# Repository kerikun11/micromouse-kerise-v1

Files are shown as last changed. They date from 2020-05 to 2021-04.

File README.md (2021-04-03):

# MicroMouse KERISE v1

クラッシクサイズマイクロマウス

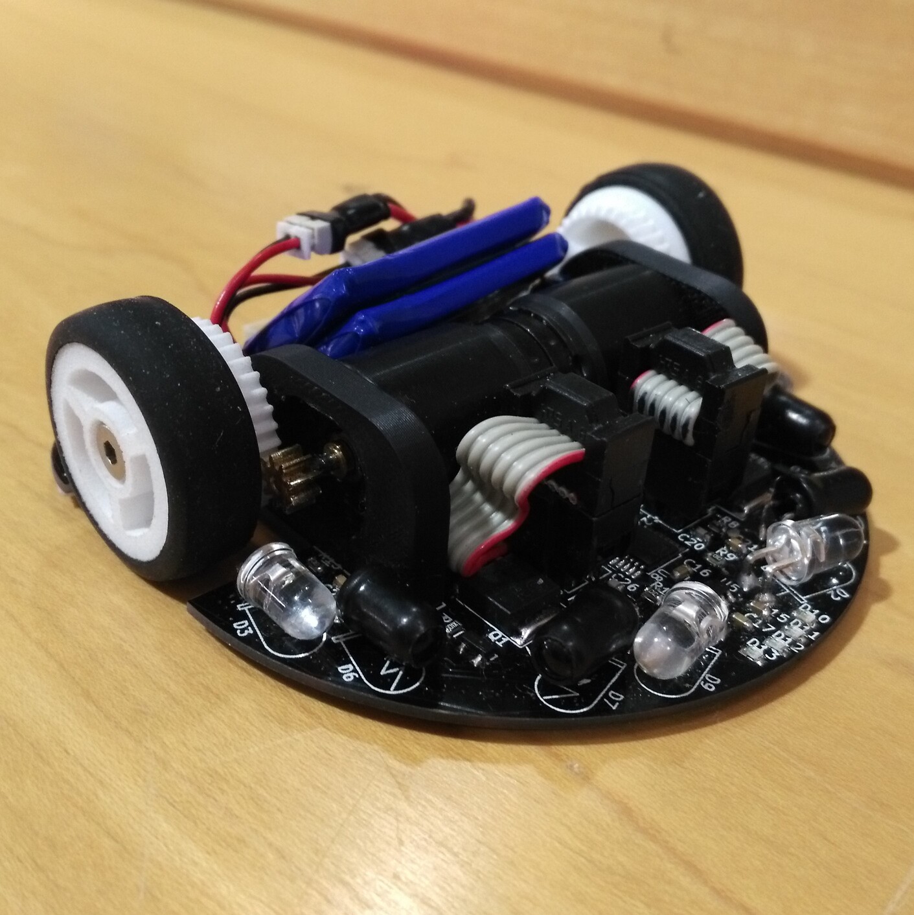
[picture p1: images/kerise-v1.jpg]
KERISE v1


## 戦績

- 第37回全日本マイクロマウス大会2016
  - クラッシック競技フレッシュマンクラス予選10位
  - クラッシック競技フレッシュマンクラス決勝9位

## スペック

| 部品 | 型番 | 備考 |
| :--- | :--- | :--- |
| モーター | 1717T006SR | 17mm x 17mm |
| エンコーダ | IEH2-1024 | 1024パルス モーター直結 |
| マイコン | STM32F405RG | 168MHz |
| 赤外線LED | VSLY5850 | 波長850mm 直径5mm |
| フォトダイオード | SFH213FA | 波長900nm 直径5mm |
| モータードライバ | DRV8835 | 最大電流3A |
| 6軸センサ | MPU6500 | 3軸ジャイロ+3軸加速度 |
| バッテリー | LG325-0120-1S-M | 3.7V 25C 120mAh 1S |

## 回路設計

- KiCad

## 開発環境

- mbed RTOS

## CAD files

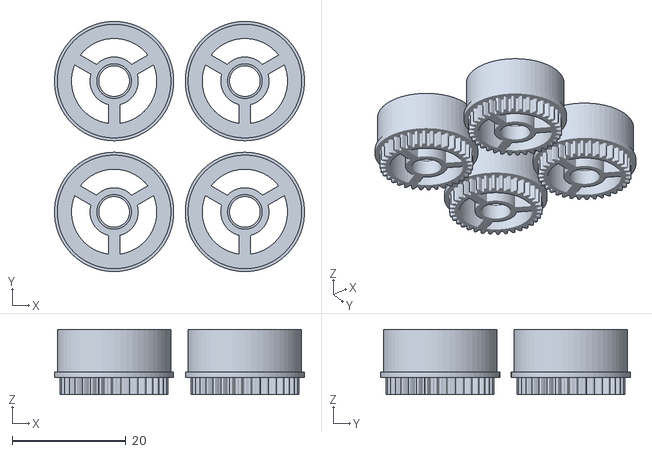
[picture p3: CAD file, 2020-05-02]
3dprint/wheel-2set.stl
44.0 x 44.0 x 11.5

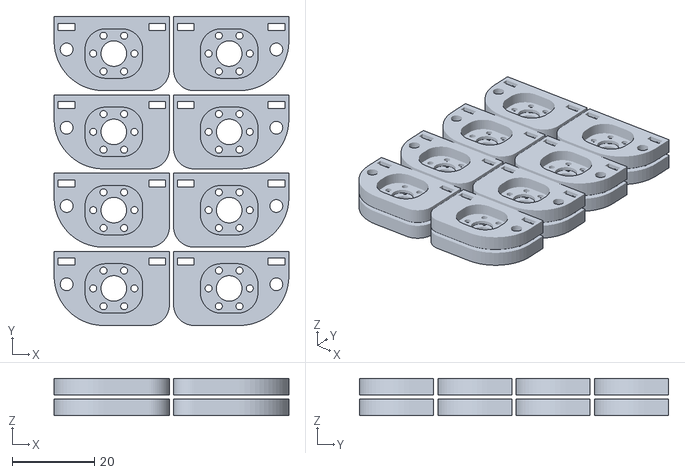
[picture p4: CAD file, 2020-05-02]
3dprint/mounter-8set.stl
57.0 x 75.0 x 9.00

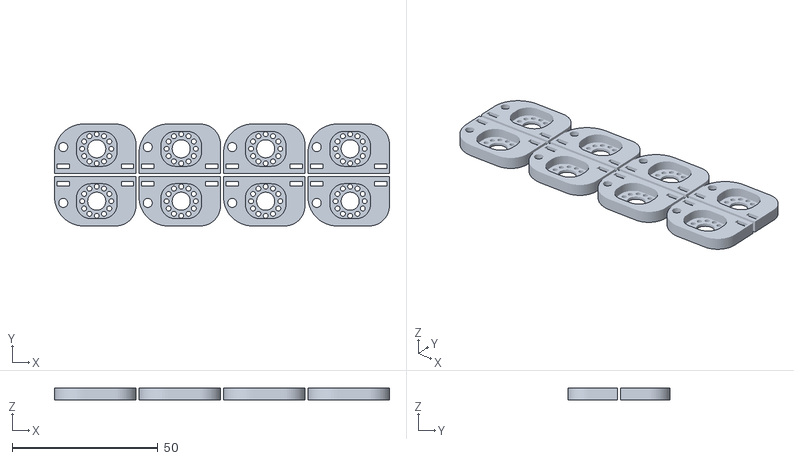
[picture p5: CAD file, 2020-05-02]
3dprint/mounter-4set.stl
115.0 x 35.0 x 4.00

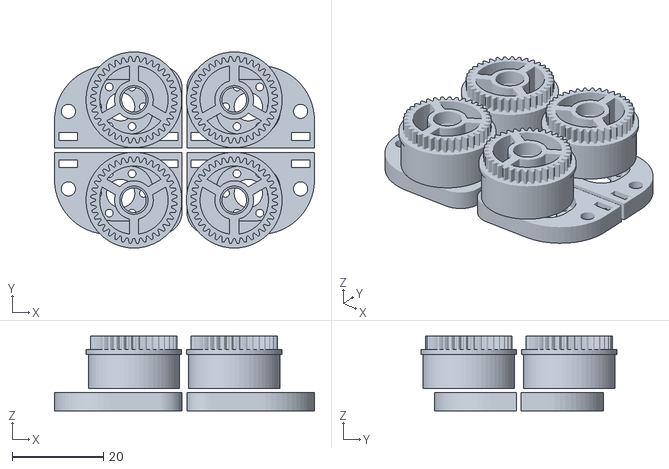
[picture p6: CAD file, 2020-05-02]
3dprint/both-2set.stl
57.0 x 43.0 x 16.4

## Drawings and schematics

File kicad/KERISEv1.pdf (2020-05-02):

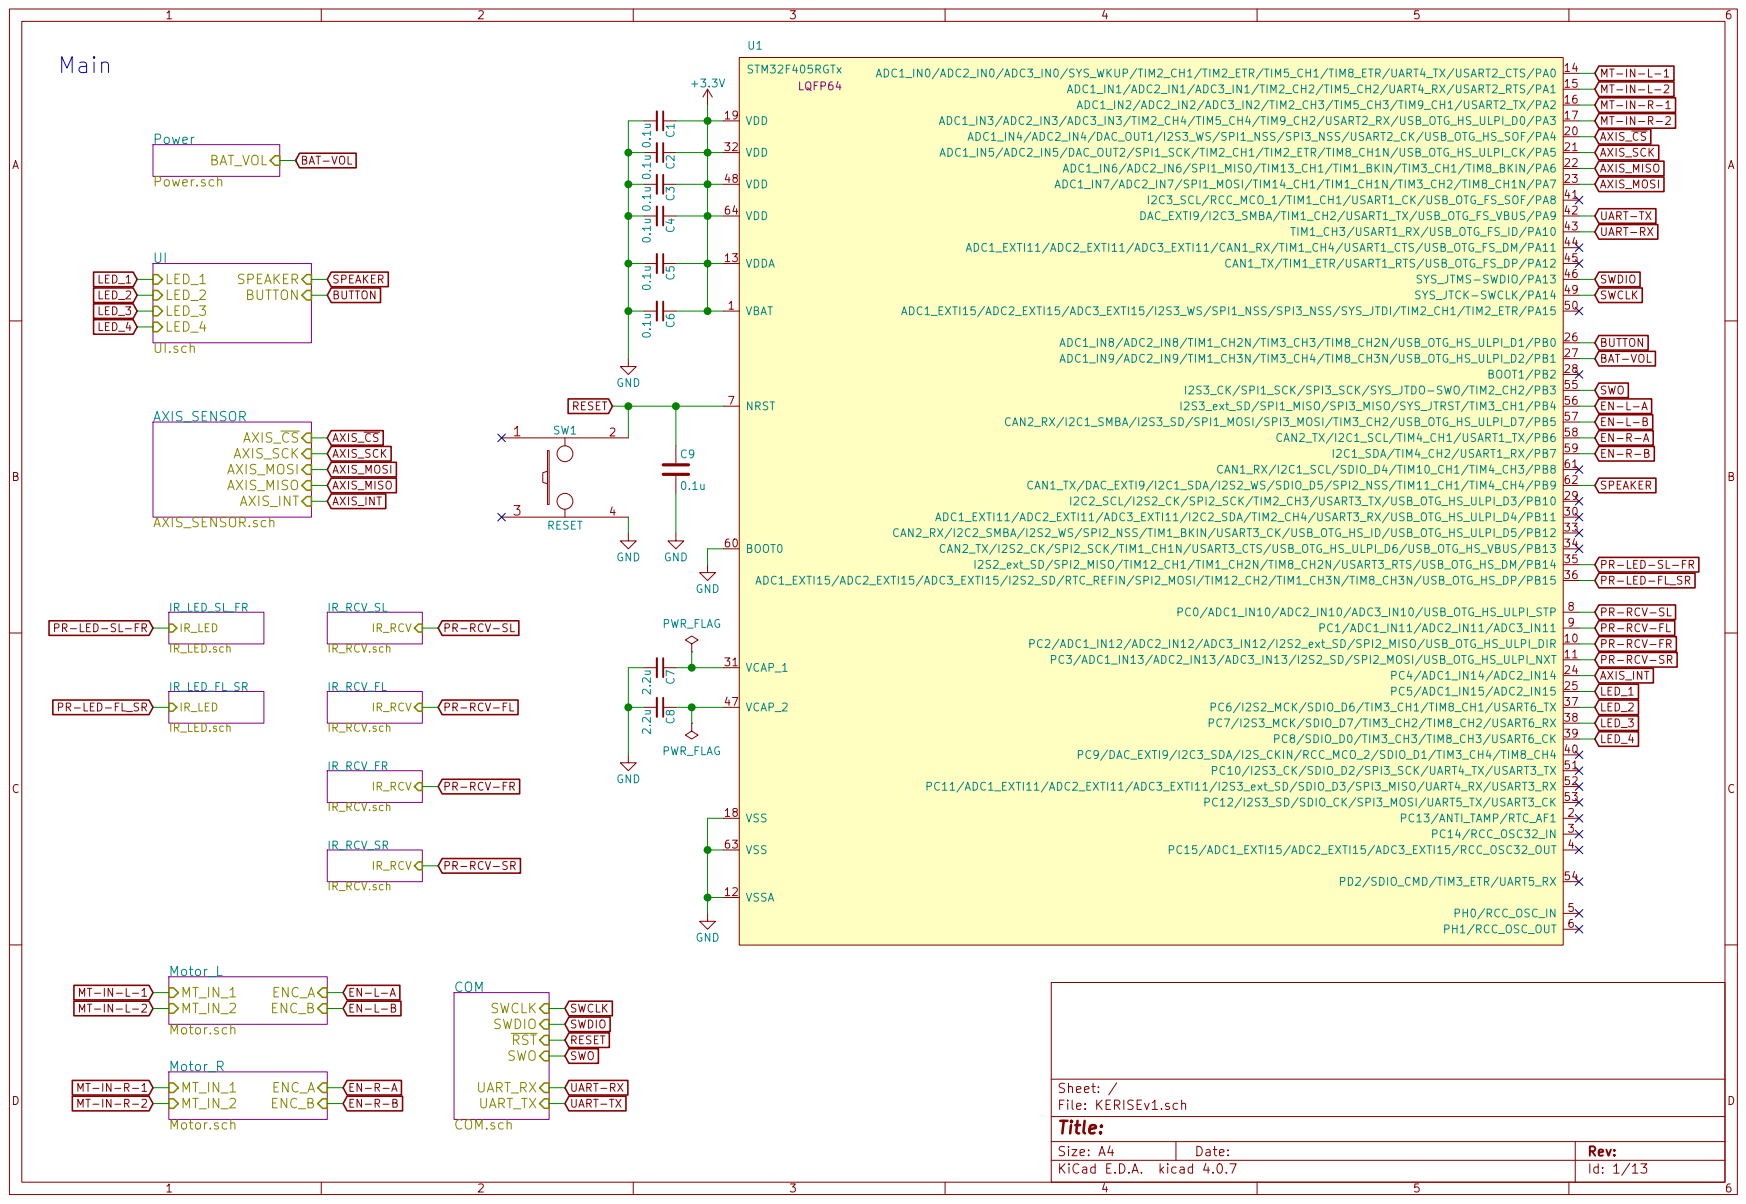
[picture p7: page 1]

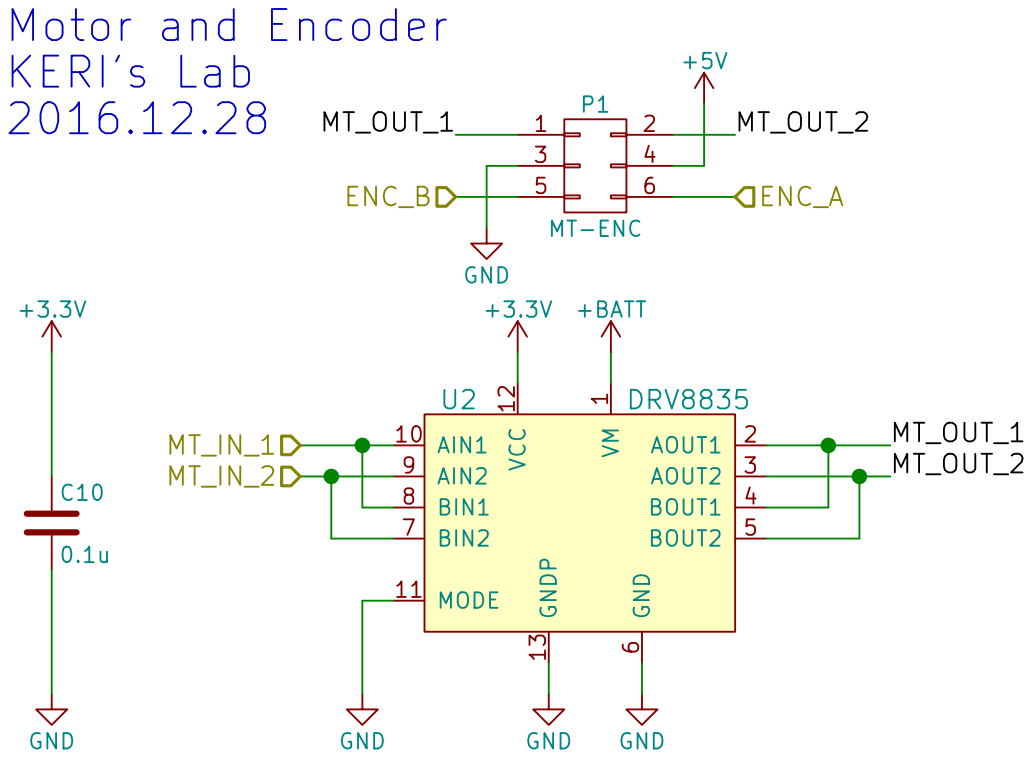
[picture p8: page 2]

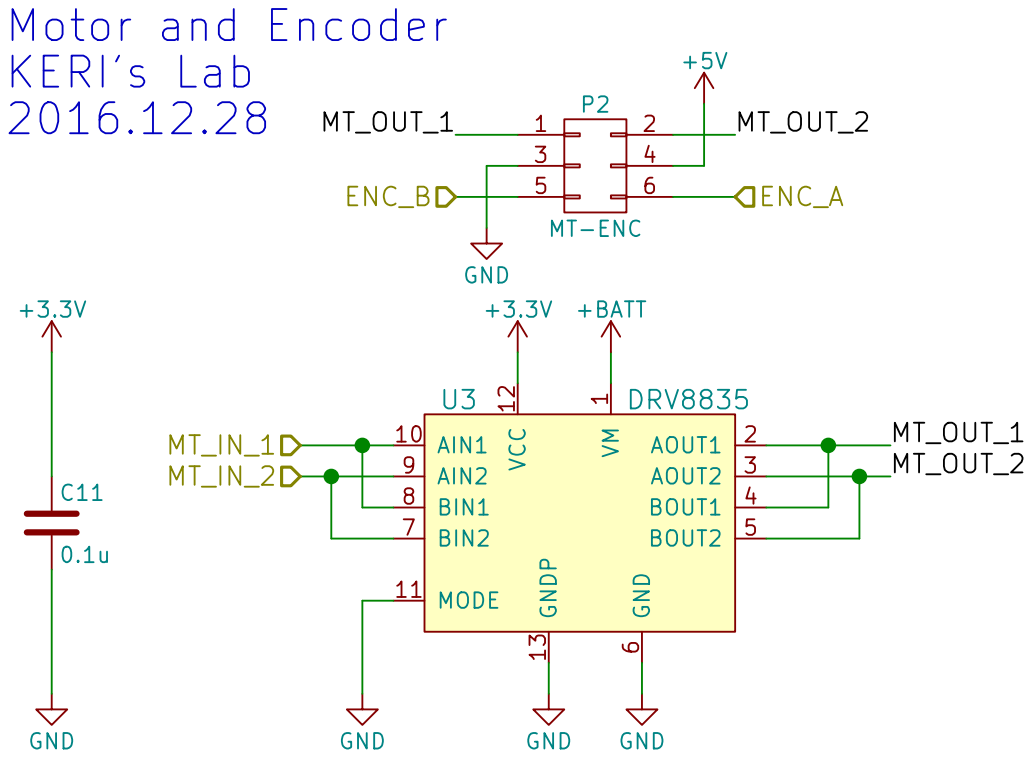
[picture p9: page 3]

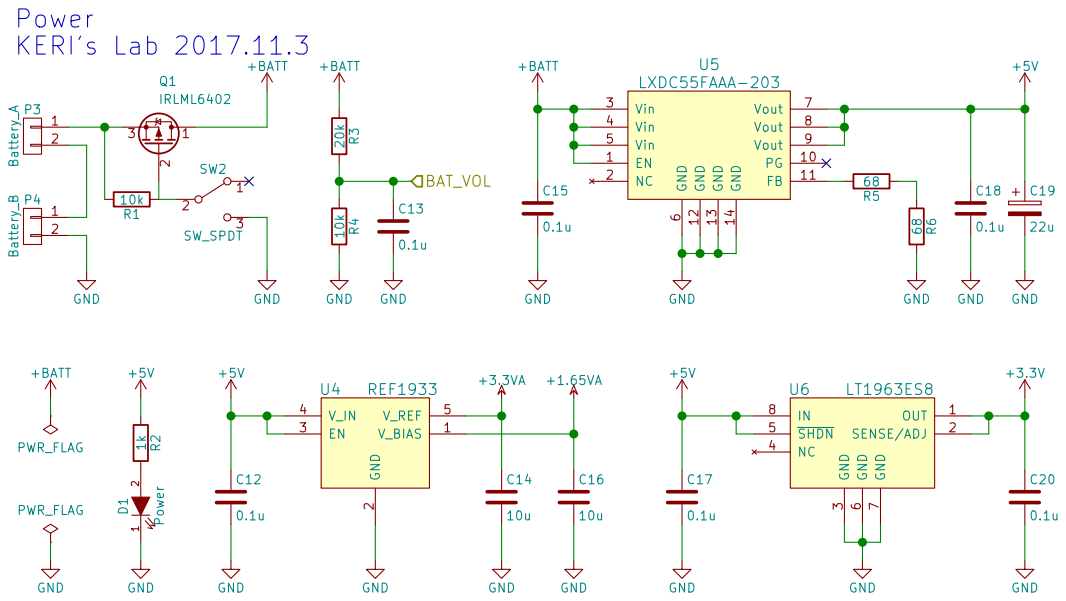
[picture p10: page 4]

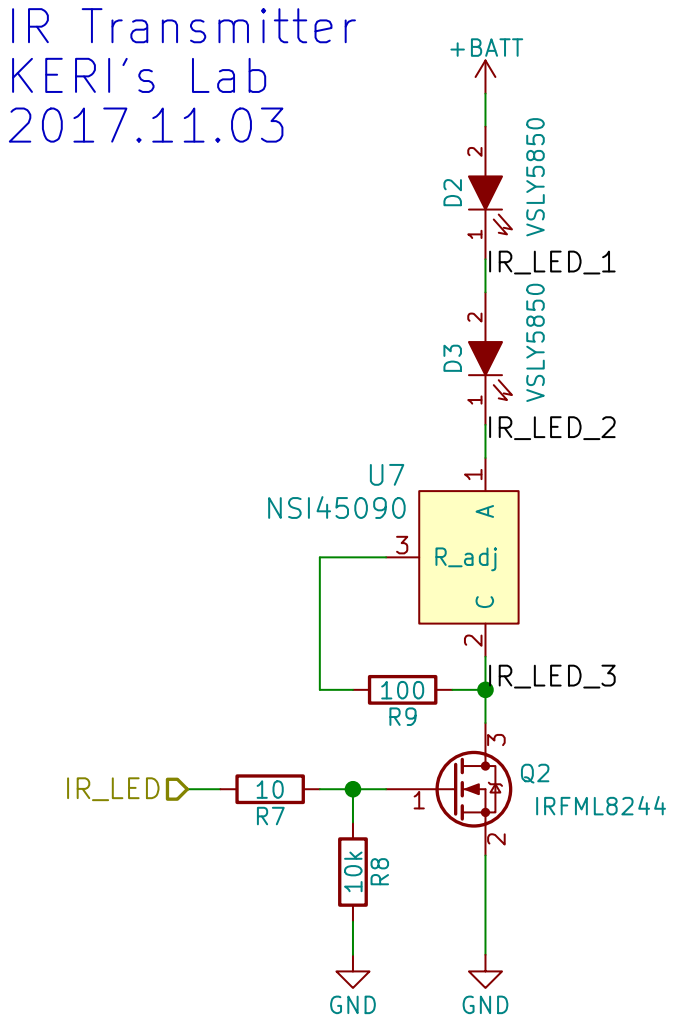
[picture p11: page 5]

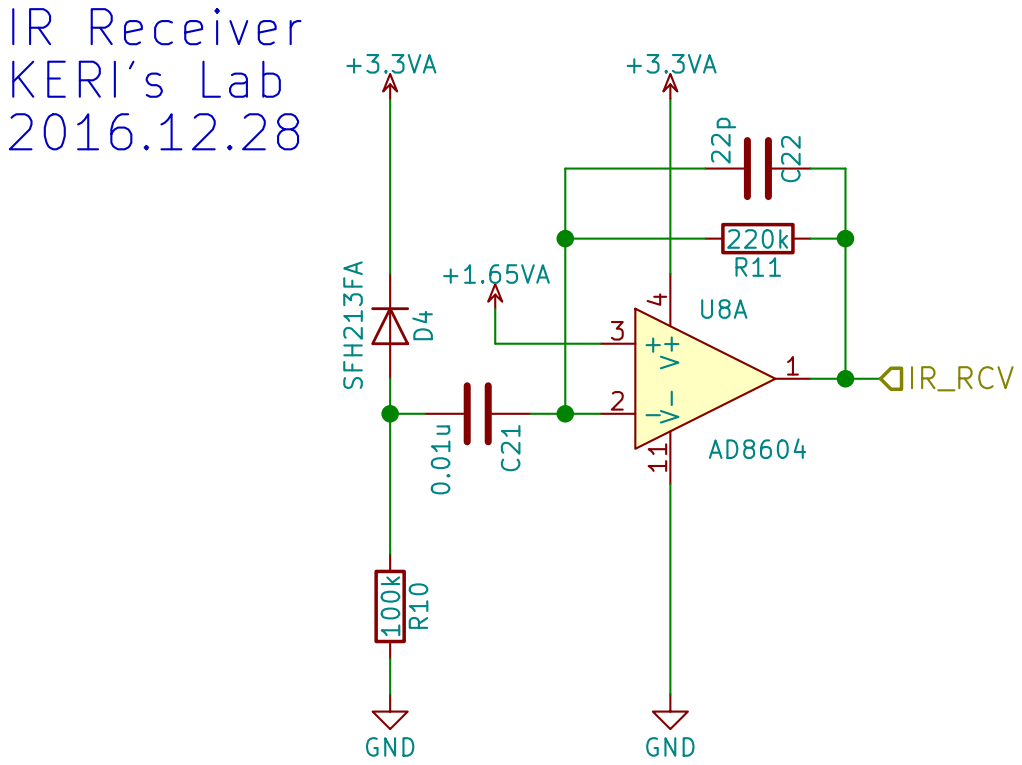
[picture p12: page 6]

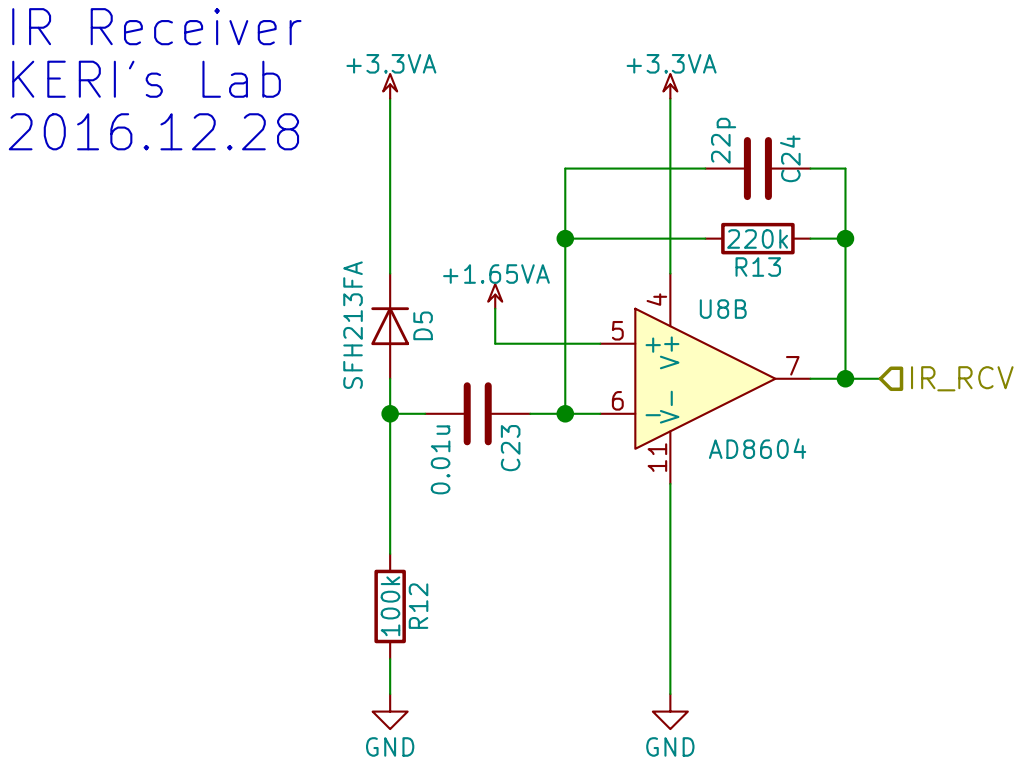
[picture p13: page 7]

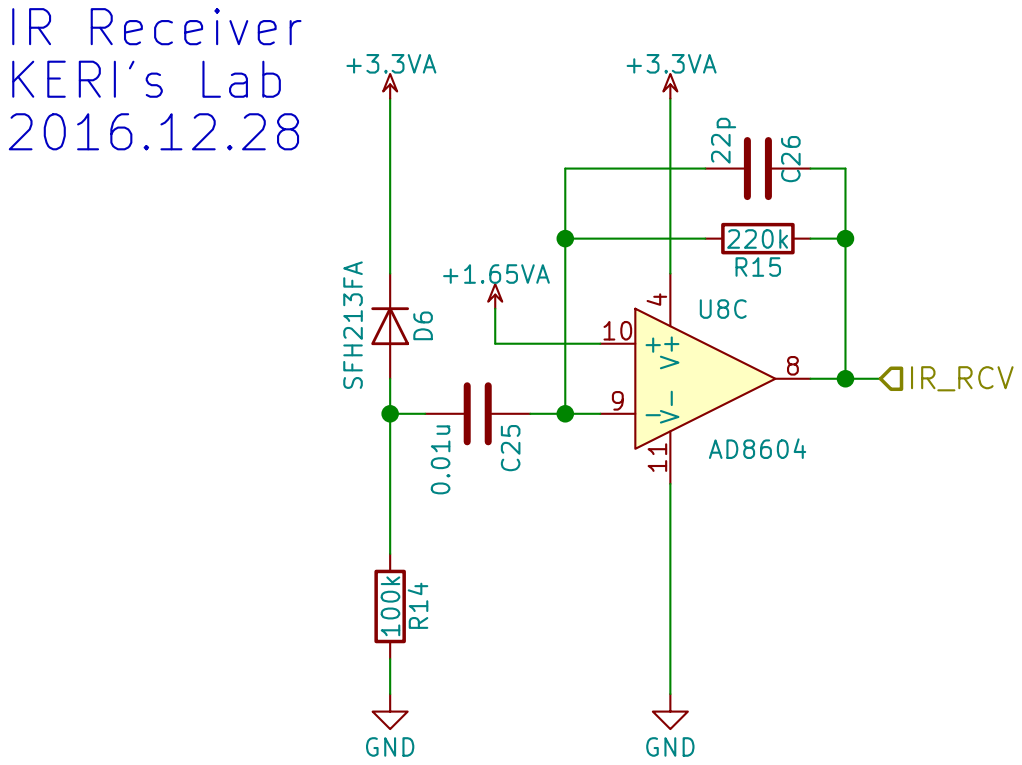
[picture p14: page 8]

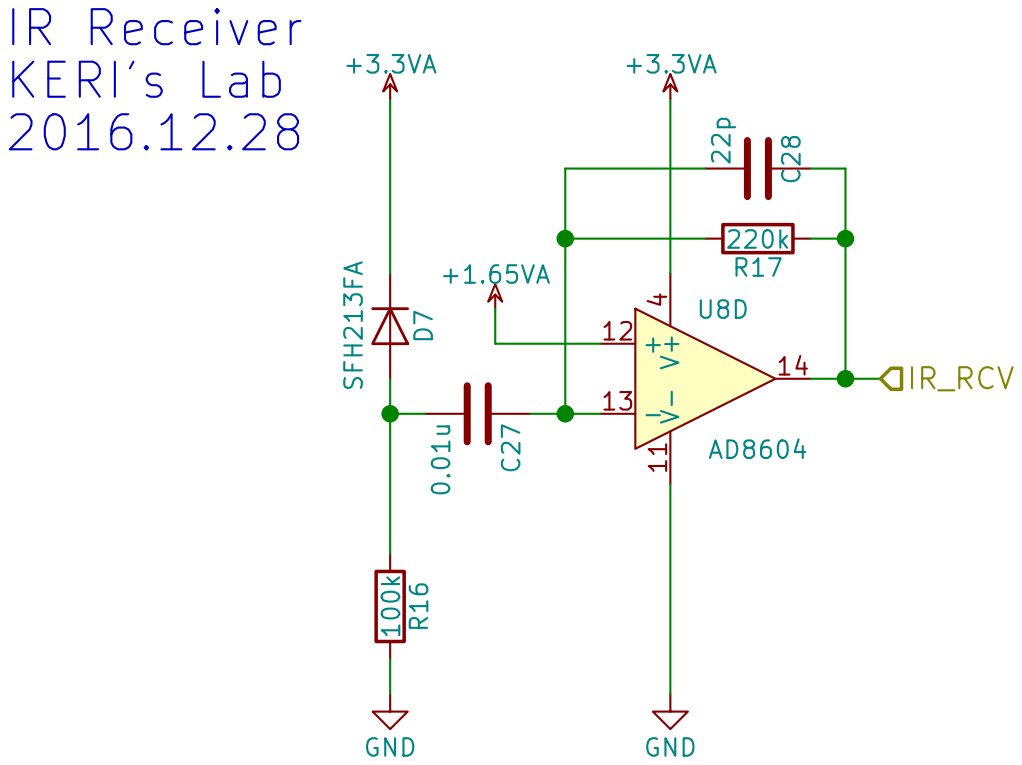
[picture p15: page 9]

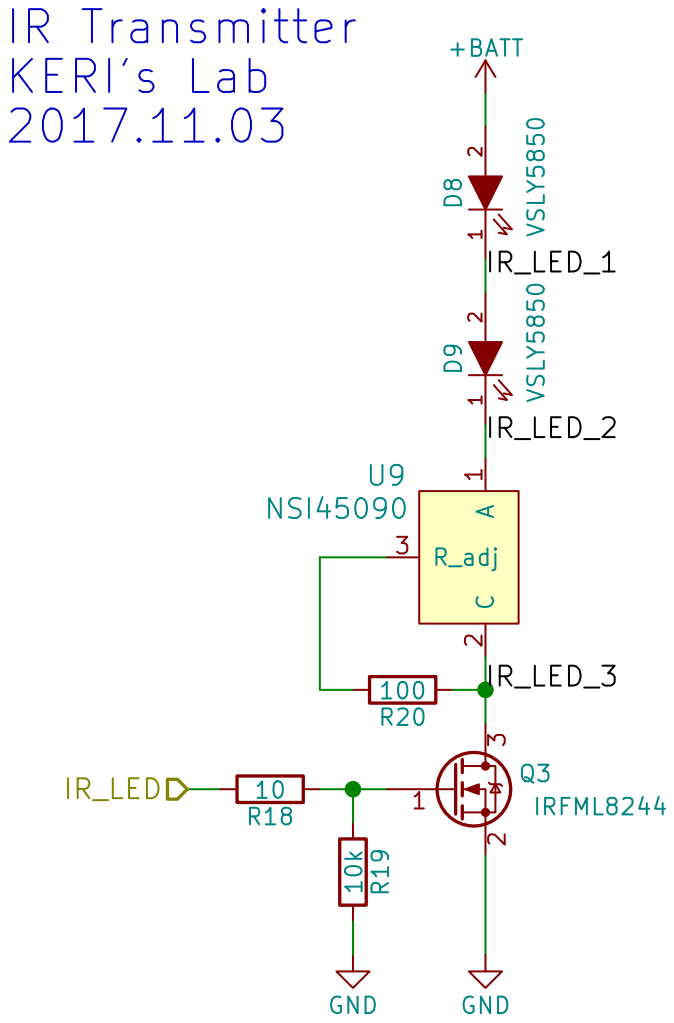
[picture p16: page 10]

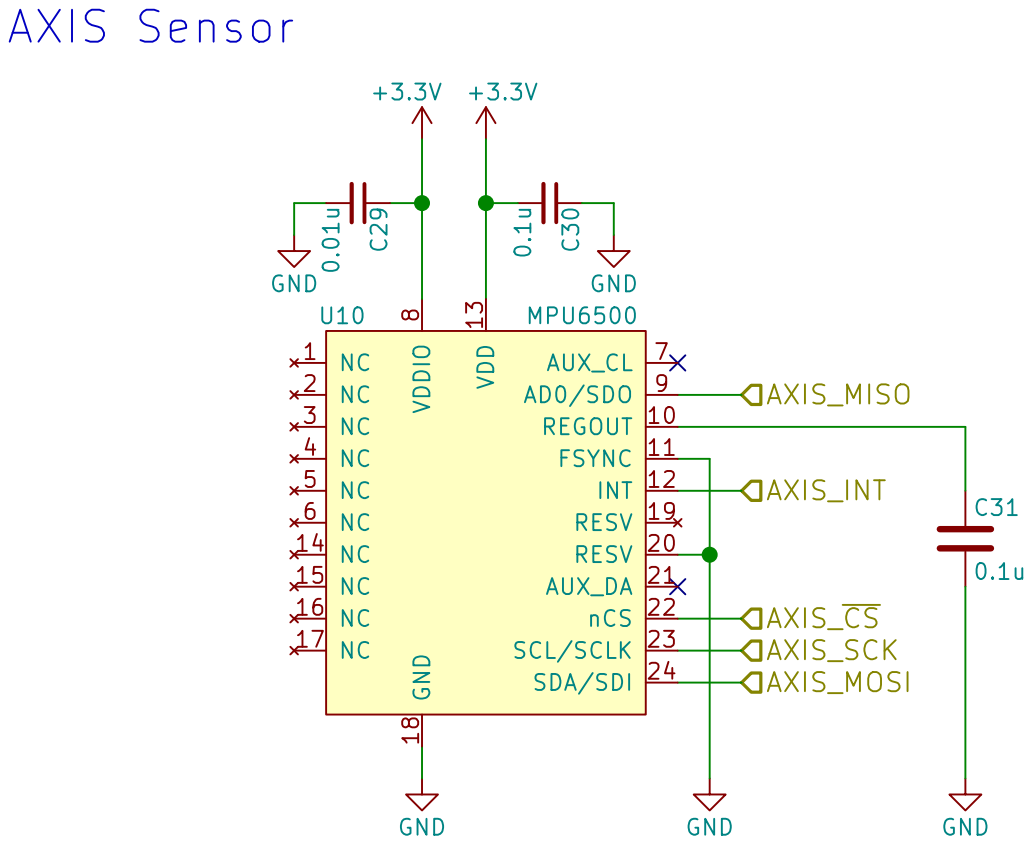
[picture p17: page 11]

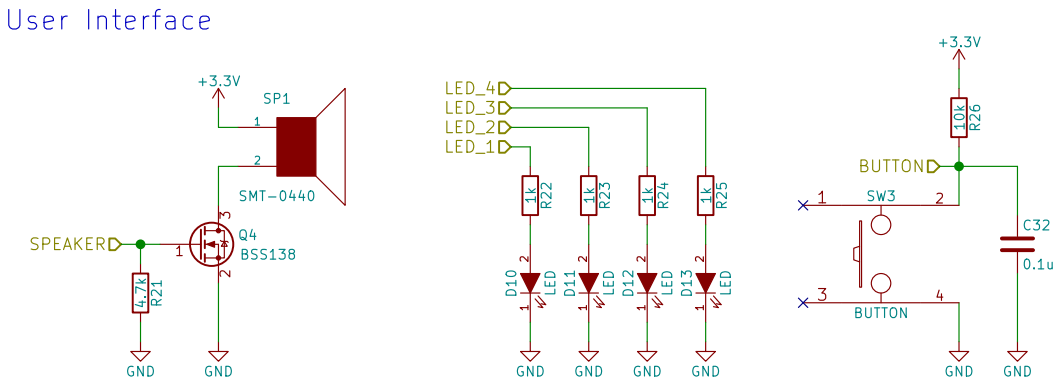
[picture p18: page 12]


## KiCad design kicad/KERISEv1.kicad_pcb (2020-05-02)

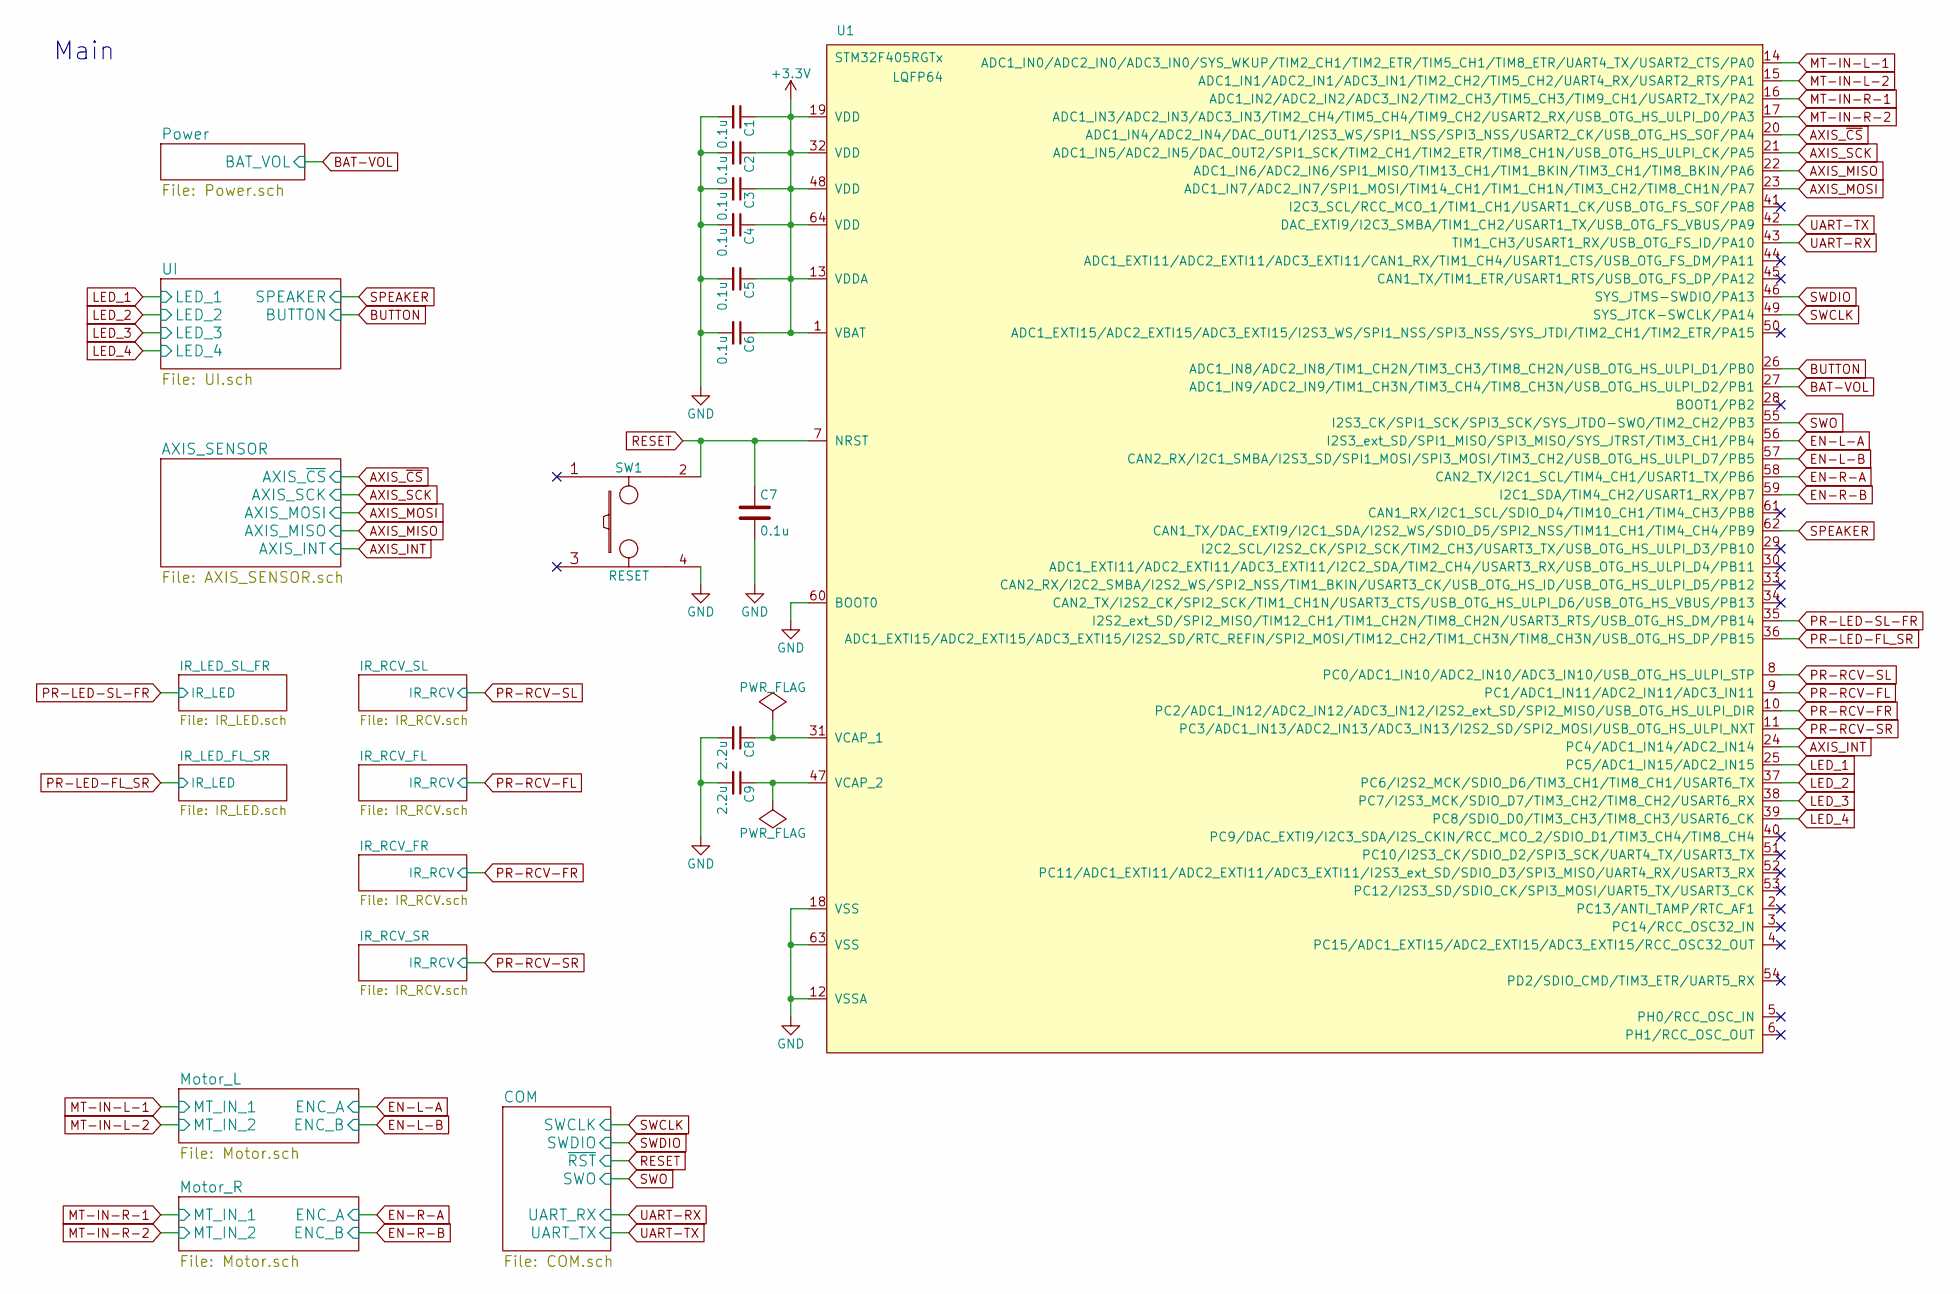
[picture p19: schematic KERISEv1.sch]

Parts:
C1, C2, C3, C4, C5, C6, C7: 0.1u; C_0603
C8, C9: 2.2u; C_0603
SW1: RESET; SKRPACE010
U1: STM32F405RGTx; LQFP64

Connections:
+3V3: C1.1, C2.1, C3.1, C4.1, C5.1, C6.1, U1.1 (VBAT), U1.13 (VDDA), U1.19 (VDD), U1.32 (VDD), U1.48 (VDD), U1.64 (VDD); also elsewhere on the board
AXIS_INT: U1.24 (PC4/ADC1_IN14/ADC2_IN14); also elsewhere on the board
AXIS_MISO: U1.22 (ADC1_IN6/ADC2_IN6/SPI1_MISO/TIM13_CH1/T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); also elsewhere on the board
AXIS_MOSI: U1.23 (ADC1_IN7/ADC2_IN7/SPI1_MOSI/TIM14_CH1/T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); also elsewhere on the board
AXIS_SCK: U1.21 (ADC1_IN5/ADC2_IN5/DAC_OUT2/SPI1_SCK/TIM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); also elsewhere on the board
AXIS_~CS: U1.20 (ADC1_IN4/ADC2_IN4/DAC_OUT1/I2S3_WS/SPI1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); also elsewhere on the board
BAT-VOL: U1.27 (ADC1_IN9/ADC2_IN9/TIM1_CH3N/TIM3_CH4/TI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); also elsewhere on the board
BUTTON: U1.26 (ADC1_IN8/ADC2_IN8/TIM1_CH2N/TIM3_CH3/TI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); also elsewhere on the board
EN-L-A: U1.56 (I2S3_ext_SD/SPI1_MISO/SPI3_MISO/SYS_JTR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); also elsewhere on the board
EN-L-B: U1.57 (CAN2_RX/I2C1_SMBA/I2S3_SD/SPI1_MOSI/SPI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); also elsewhere on the board
EN-R-A: U1.58 (CAN2_TX/I2C1_SCL/TIM4_CH1/USART1_TX/PB6); also elsewhere on the board
EN-R-B: U1.59 (I2C1_SDA/TIM4_CH2/USART1_RX/PB7); also elsewhere on the board
GND: C1.2, C2.2, C3.2, C4.2, C5.2, C6.2, C7.2, C8.2, C9.2, SW1.4, U1.12 (VSSA), U1.18 (VSS), U1.60 (BOOT0), U1.63 (VSS); also elsewhere on the board
LED_1: U1.25 (PC5/ADC1_IN15/ADC2_IN15); also elsewhere on the board
LED_2: U1.37 (PC6/I2S2_MCK/SDIO_D6/TIM3_CH1/TIM8_CH1/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); also elsewhere on the board
LED_3: U1.38 (PC7/I2S3_MCK/SDIO_D7/TIM3_CH2/TIM8_CH2/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); also elsewhere on the board
LED_4: U1.39 (PC8/SDIO_D0/TIM3_CH3/TIM8_CH3/USART6_CK); also elsewhere on the board
MT-IN-L-1: U1.14 (ADC1_IN0/ADC2_IN0/ADC3_IN0/SYS_WKUP/TIM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); also elsewhere on the board
MT-IN-L-2: U1.15 (ADC1_IN1/ADC2_IN1/ADC3_IN1/TIM2_CH2/TIM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); also elsewhere on the board
MT-IN-R-1: U1.16 (ADC1_IN2/ADC2_IN2/ADC3_IN2/TIM2_CH3/TIM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); also elsewhere on the board
MT-IN-R-2: U1.17 (ADC1_IN3/ADC2_IN3/ADC3_IN3/TIM2_CH4/TIM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); also elsewhere on the board
unnamed: C8.1, U1.31 (VCAP_1)
unnamed: C9.1, U1.47 (VCAP_2)
PR-LED-FL_SR: U1.36 (ADC1_EXTI15/ADC2_EXTI15/ADC3_EXTI15/I2S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); also elsewhere on the board
PR-LED-SL-FR: U1.35 (I2S2_ext_SD/SPI2_MISO/TIM12_CH1/TIM1_CH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); also elsewhere on the board
PR-RCV-FL: U1.9 (PC1/ADC1_IN11/ADC2_IN11/ADC3_IN11); also elsewhere on the board
PR-RCV-FR: U1.10 (PC2/ADC1_IN12/ADC2_IN12/ADC3_IN12/I2S2_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); also elsewhere on the board
PR-RCV-SL: U1.8 (PC0/ADC1_IN10/ADC2_IN10/ADC3_IN10/USB_O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); also elsewhere on the board
PR-RCV-SR: U1.11 (PC3/ADC1_IN13/ADC2_IN13/ADC3_IN13/I2S2_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); also elsewhere on the board
RESET: C7.1, SW1.2, U1.7 (NRST); also elsewhere on the board
SPEAKER: U1.62 (CAN1_TX/DAC_EXTI9/I2C1_SDA/I2S2_WS/SDIO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); also elsewhere on the board
SWCLK: U1.49 (SYS_JTCK-SWCLK/PA14); also elsewhere on the board
SWDIO: U1.46 (SYS_JTMS-SWDIO/PA13); also elsewhere on the board
SWO: U1.55 (I2S3_CK/SPI1_SCK/SPI3_SCK/SYS_JTDO-SWO/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); also elsewhere on the board
UART-RX: U1.43 (TIM1_CH3/USART1_RX/USB_OTG_FS_ID/PA10); also elsewhere on the board
UART-TX: U1.42 (DAC_EXTI9/I2C3_SMBA/TIM1_CH2/USART1_TX/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); also elsewhere on the board

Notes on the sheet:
Main

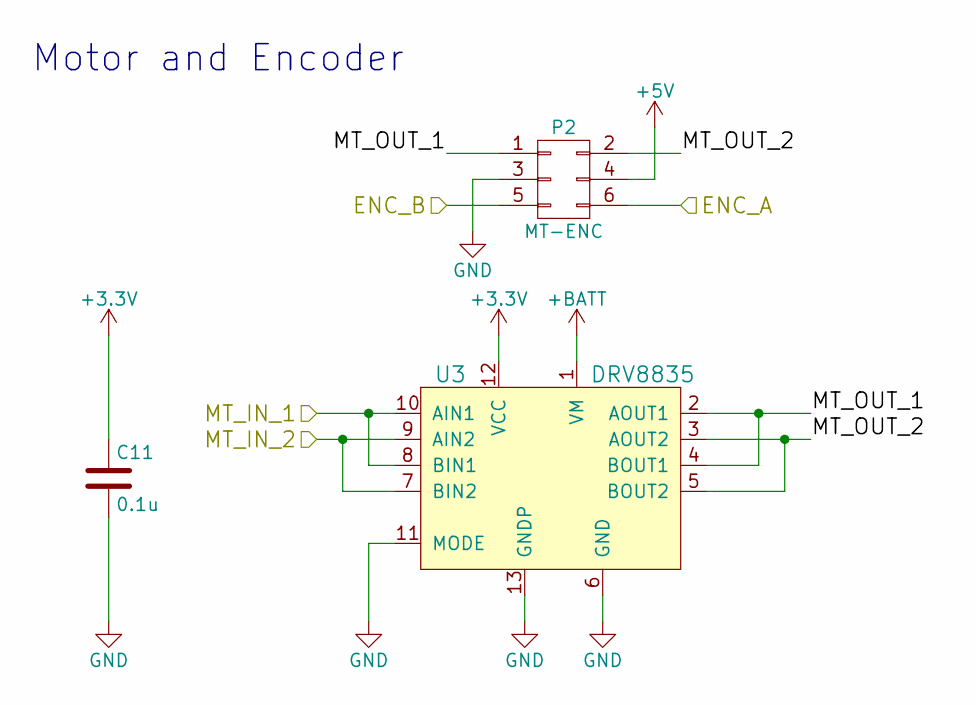
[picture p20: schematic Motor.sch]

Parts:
C10: 0.1u; C_0603
P1: MT-ENC; Pin_Header_Straight_2x03
U2: DRV8835

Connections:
+3V3: C10.1, U2.12 (VCC); also elsewhere on the board
+5V: P1.4; also elsewhere on the board
+BATT: U2.1 (VM); also elsewhere on the board
/Motor_L/MT_OUT_1: P1.1, U2.2 (AOUT1), U2.4 (BOUT1)
/Motor_L/MT_OUT_2: P1.2, U2.3 (AOUT2), U2.5 (BOUT2)
EN-L-A: P1.6; also elsewhere on the board
EN-L-B: P1.5; also elsewhere on the board
GND: C10.2, P1.3, U2.6 (GND), U2.11 (MODE), U2.13 (GNDP); also elsewhere on the board
MT-IN-L-1: U2.8 (BIN1), U2.10 (AIN1); also elsewhere on the board
MT-IN-L-2: U2.7 (BIN2), U2.9 (AIN2); also elsewhere on the board

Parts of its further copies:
C11: 0.1u; C_0603
P2: MT-ENC; Pin_Header_Straight_2x03
U3: DRV8835

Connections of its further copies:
+3V3: C11.1, U3.12 (VCC); also elsewhere on the board
+5V: P2.4; also elsewhere on the board
+BATT: U3.1 (VM); also elsewhere on the board
/Motor_R/MT_OUT_1: P2.1, U3.2 (AOUT1), U3.4 (BOUT1)
/Motor_R/MT_OUT_2: P2.2, U3.3 (AOUT2), U3.5 (BOUT2)
EN-R-A: P2.6; also elsewhere on the board
EN-R-B: P2.5; also elsewhere on the board
GND: C11.2, P2.3, U3.6 (GND), U3.11 (MODE), U3.13 (GNDP); also elsewhere on the board
MT-IN-R-1: U3.8 (BIN1), U3.10 (AIN1); also elsewhere on the board
MT-IN-R-2: U3.7 (BIN2), U3.9 (AIN2); also elsewhere on the board

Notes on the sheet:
Motor and Encoder

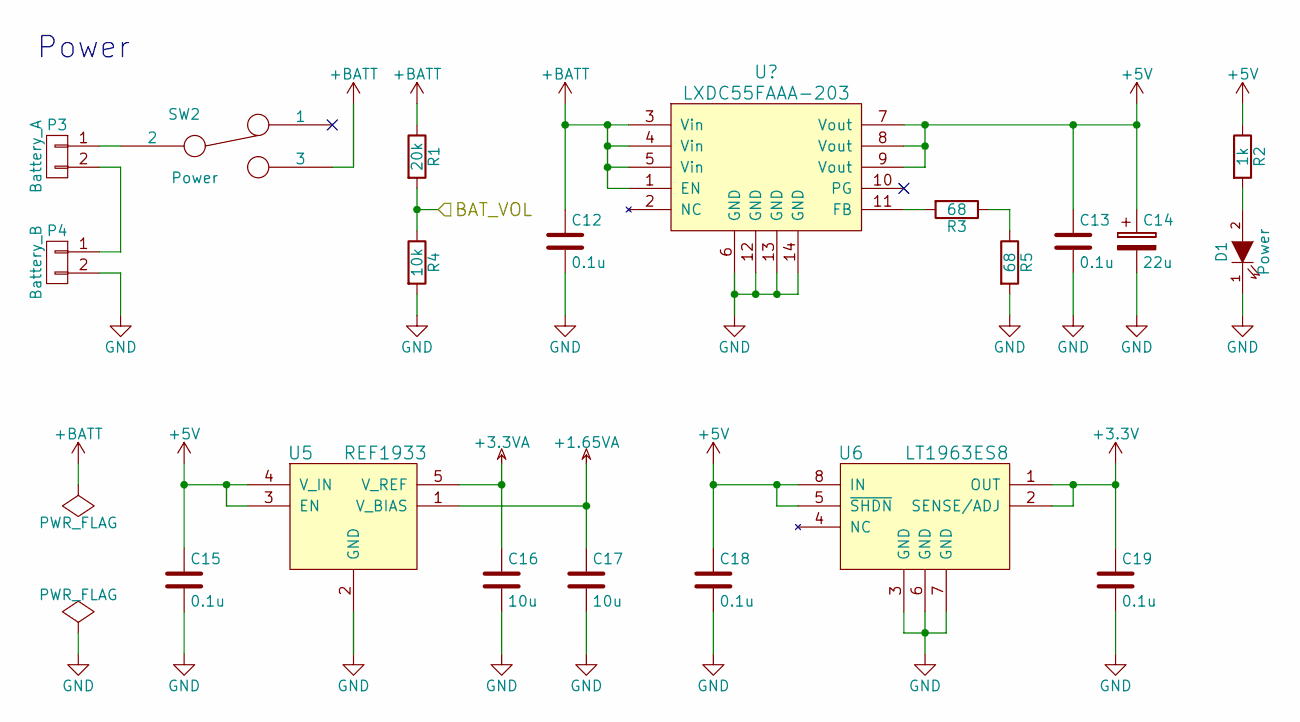
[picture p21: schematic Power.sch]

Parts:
C12, C13, C15, C18, C19: 0.1u; C_0603
C14: 22u; C_0805
C16, C17: 10u; C_0603
D1: Power; LED_0603
P3: Battery_A; JST_PH_B2B-PH-K_02x2.00mm_Straight
P4: Battery_B; JST_PH_B2B-PH-K_02x2.00mm_Straight
R1: 20k; R_0603
R2: 1k; R_0603
R3, R5: 68; R_0603
R4: 10k; R_0603
SW2: Power; Pin_Header_Straight_1x03
U5: REF1933; SOT-23-5
U6: LT1963ES8; SOIC-8_3.9x4.9mm_Pitch1.27mm

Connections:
+1.65VA: C17.1, U5.1 (V_BIAS); also elsewhere on the board
+3.3VADC: C16.1, U5.5 (V_REF); also elsewhere on the board
+3V3: C19.1, U6.1 (OUT), U6.2 (SENSE/ADJ); also elsewhere on the board
+5V: C13.1, C14.1, C15.1, C18.1, R2.1, U5.3 (EN), U5.4 (V_IN), U6.5 (~SHDN), U6.8 (IN); also elsewhere on the board
+BATT: C12.1, R1.1, SW2.3; also elsewhere on the board
BAT-VOL: R1.2, R4.1; also elsewhere on the board
GND: C12.2, C13.2, C14.2, C15.2, C16.2, C17.2, C18.2, C19.2, D1.1 (K), P4.2, R4.2, R5.2, U5.2 (GND), U6.3 (GND), U6.6 (GND), U6.7 (GND); also elsewhere on the board
unnamed: D1.2 (A), R2.2
unnamed: P3.1, SW2.2
unnamed: P3.2, P4.1
unnamed: R3.1, R5.1
unnamed 57: R3.2; also elsewhere on the board

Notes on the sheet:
Power

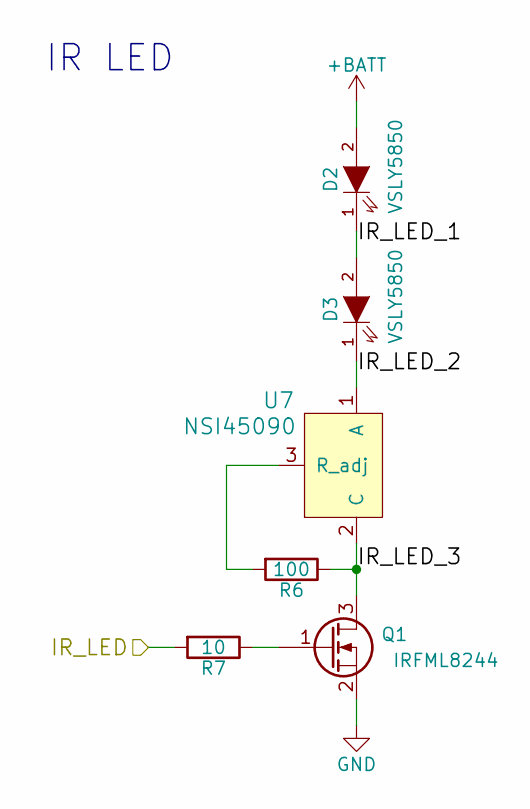
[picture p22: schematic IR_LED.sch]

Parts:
D2, D3: VSLY5850; LED-5MM_Angle
Q1: IRFML8244; SOT-23
R6: 100; R_0603
R7: 10; R_0603
U7: NSI45090; TO-252-2Lead

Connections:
+BATT: D2.2 (A); also elsewhere on the board
/IR_LED_SL_FR/IR_LED_1: D2.1 (K), D3.2 (A)
/IR_LED_SL_FR/IR_LED_2: D3.1 (K), U7.1 (A)
/IR_LED_SL_FR/IR_LED_3: Q1.3 (D), R6.1, U7.2 (C)
GND: Q1.2 (S); also elsewhere on the board
unnamed: Q1.1 (G), R7.1
unnamed: R6.2, U7.3 (R_adj)
PR-LED-SL-FR: R7.2; also elsewhere on the board

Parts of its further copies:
D8, D9: VSLY5850; LED-5MM_Angle
Q2: IRFML8244; SOT-23
R16: 100; R_0603
R17: 10; R_0603
U9: NSI45090; TO-252-2Lead

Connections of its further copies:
+BATT: D8.2 (A); also elsewhere on the board
/IR_LED_FL_SR/IR_LED_1: D8.1 (K), D9.2 (A)
/IR_LED_FL_SR/IR_LED_2: D9.1 (K), U9.1 (A)
/IR_LED_FL_SR/IR_LED_3: Q2.3 (D), R16.1, U9.2 (C)
GND: Q2.2 (S); also elsewhere on the board
unnamed: Q2.1 (G), R17.1
unnamed: R16.2, U9.3 (R_adj)
PR-LED-FL_SR: R17.2; also elsewhere on the board

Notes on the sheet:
IR LED

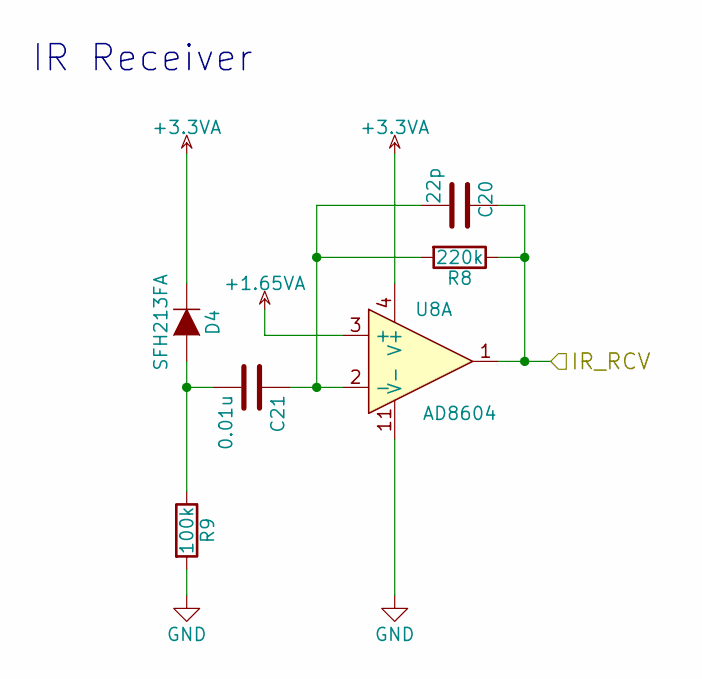
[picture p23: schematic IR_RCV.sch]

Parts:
C20: 22p; C_0603
C21: 0.01u; C_0603
D4: SFH213FA; Photo-5MM_Angle
R8: 220k; R_0603
R9: 100k; R_0603
U8: AD8604; TSSOP-14_4.4x5mm_Pitch0.65mm

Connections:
+1.65VA: U8.3 (+), U8.5 (+), U8.10 (+), U8.12 (+); also elsewhere on the board
+3.3VADC: D4.1 (K), U8.4 (V+); also elsewhere on the board
GND: R9.2, U8.11 (V-); also elsewhere on the board
unnamed: C20.2, C21.1, R8.2, U8.2 (-)
unnamed: C21.2, D4.2 (A), R9.1
unnamed 39: U8.6 (-); also elsewhere on the board
unnamed 41: U8.9 (-); also elsewhere on the board
unnamed 43: U8.13 (-); also elsewhere on the board
PR-RCV-FL: U8.7; also elsewhere on the board
PR-RCV-FR: U8.8; also elsewhere on the board
PR-RCV-SL: C20.1, R8.1, U8.1; also elsewhere on the board
PR-RCV-SR: U8.14; also elsewhere on the board

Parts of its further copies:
C22, C24, C26: 22p; C_0603
C23, C25, C27: 0.01u; C_0603
D5, D6, D7: SFH213FA; Photo-5MM_Angle
R10, R12, R14: 220k; R_0603
R11, R13, R15: 100k; R_0603

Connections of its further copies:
+3.3VADC: D5.1 (K), D6.1 (K), D7.1 (K); also elsewhere on the board
GND: R11.2, R13.2, R15.2; also elsewhere on the board
unnamed 39: C22.2, C23.1, R10.2; also elsewhere on the board
unnamed: C23.2, D5.2 (A), R11.1
unnamed 41: C24.2, C25.1, R12.2; also elsewhere on the board
unnamed: C25.2, D6.2 (A), R13.1
unnamed 43: C26.2, C27.1, R14.2; also elsewhere on the board
unnamed: C27.2, D7.2 (A), R15.1
PR-RCV-FL: C22.1, R10.1; also elsewhere on the board
PR-RCV-FR: C24.1, R12.1; also elsewhere on the board
PR-RCV-SR: C26.1, R14.1; also elsewhere on the board

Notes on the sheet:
IR Receiver

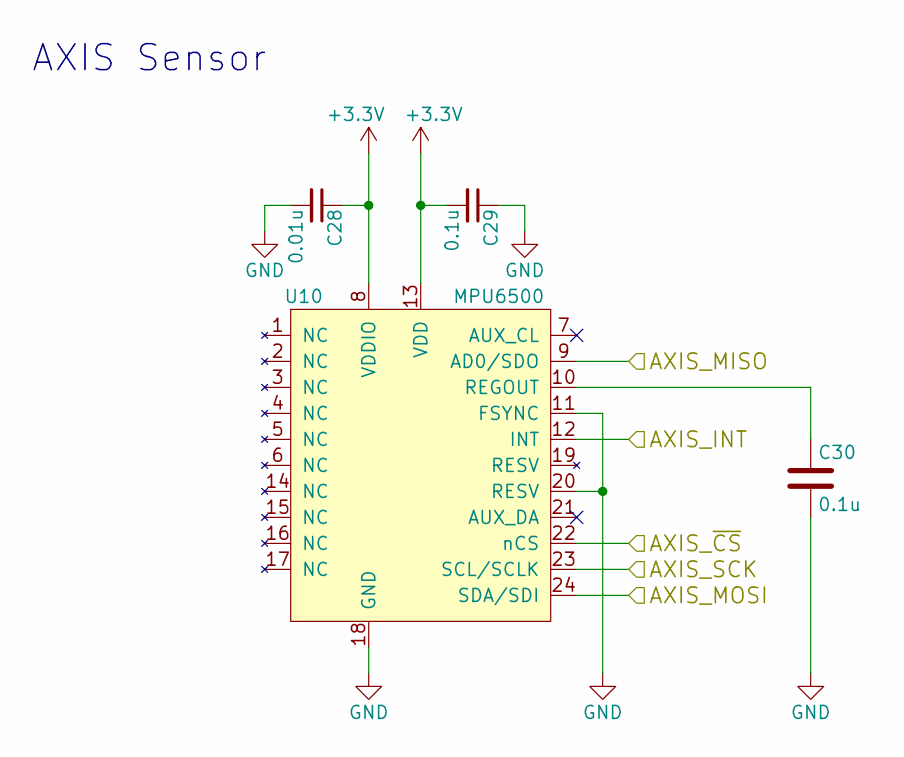
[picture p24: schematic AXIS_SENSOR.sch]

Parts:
C28: 0.01u; C_0603
C29, C30: 0.1u; C_0603
U10: MPU6500; QFN-24-1EP_3x3mm_Pitch0.4mm

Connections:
+3V3: C28.1, C29.2, U10.8 (VDDIO), U10.13 (VDD); also elsewhere on the board
AXIS_INT: U10.12 (INT); also elsewhere on the board
AXIS_MISO: U10.9 (AD0/SDO); also elsewhere on the board
AXIS_MOSI: U10.24 (SDA/SDI); also elsewhere on the board
AXIS_SCK: U10.23 (SCL/SCLK); also elsewhere on the board
AXIS_~CS: U10.22 (nCS); also elsewhere on the board
GND: C28.2, C29.1, C30.2, U10.11 (FSYNC), U10.18 (GND), U10.20 (RESV); also elsewhere on the board
unnamed: C30.1, U10.10 (REGOUT)

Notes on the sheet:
AXIS Sensor

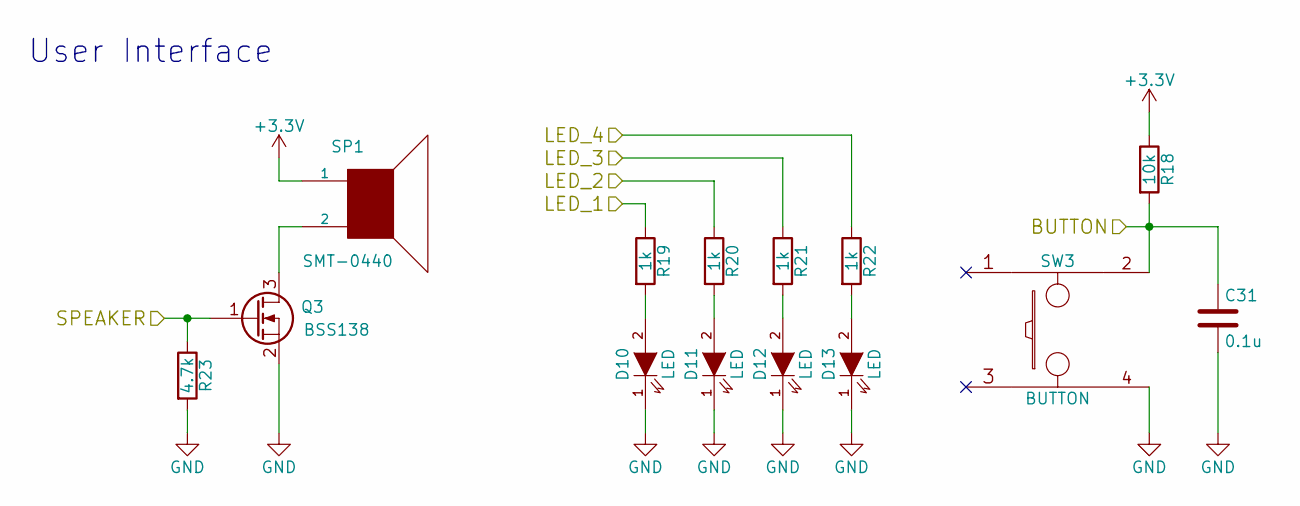
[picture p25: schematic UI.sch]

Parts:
C31: 0.1u; C_0603
D10, D11, D12, D13: LED; LED_0603
Q3: BSS138; SOT-23
R18: 10k; R_0603
R19, R20, R21, R22: 1k; R_0603
R23: 4.7k; R_0603
SP1: SMT-0440; SMT-0440-S-R
SW3: BUTTON; SKRPACE010

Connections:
+3V3: R18.1, SP1.1; also elsewhere on the board
BUTTON: C31.1, R18.2, SW3.2; also elsewhere on the board
GND: C31.2, D10.1 (K), D11.1 (K), D12.1 (K), D13.1 (K), Q3.2 (S), R23.2, SW3.4; also elsewhere on the board
LED_1: R19.1; also elsewhere on the board
LED_2: R20.1; also elsewhere on the board
LED_3: R21.1; also elsewhere on the board
LED_4: R22.1; also elsewhere on the board
unnamed: D10.2 (A), R19.2
unnamed: D11.2 (A), R20.2
unnamed: D12.2 (A), R21.2
unnamed: D13.2 (A), R22.2
unnamed: Q3.3 (D), SP1.2
SPEAKER: Q3.1 (G), R23.1; also elsewhere on the board

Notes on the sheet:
User Interface

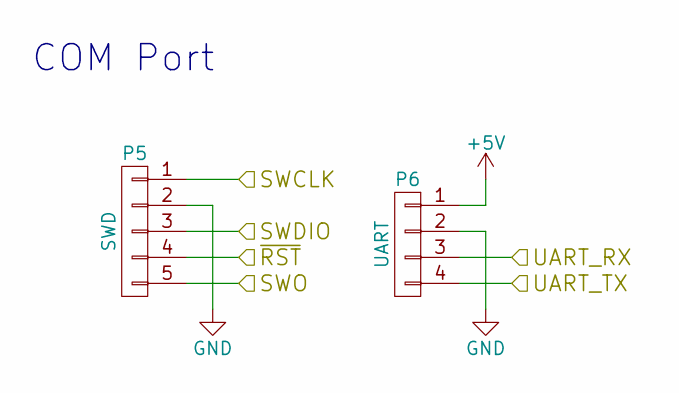
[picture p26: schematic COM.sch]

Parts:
P5: SWD; JST_SH_BM05B-SRSS-TB_05x1.00mm_Straight
P6: UART; JST_SH_BM04B-SRSS-TB_04x1.00mm_Straight

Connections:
+5V: P6.1; also elsewhere on the board
GND: P5.2, P6.2; also elsewhere on the board
RESET: P5.4; also elsewhere on the board
SWCLK: P5.1; also elsewhere on the board
SWDIO: P5.3; also elsewhere on the board
SWO: P5.5; also elsewhere on the board
UART-RX: P6.3; also elsewhere on the board
UART-TX: P6.4; also elsewhere on the board

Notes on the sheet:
COM Port

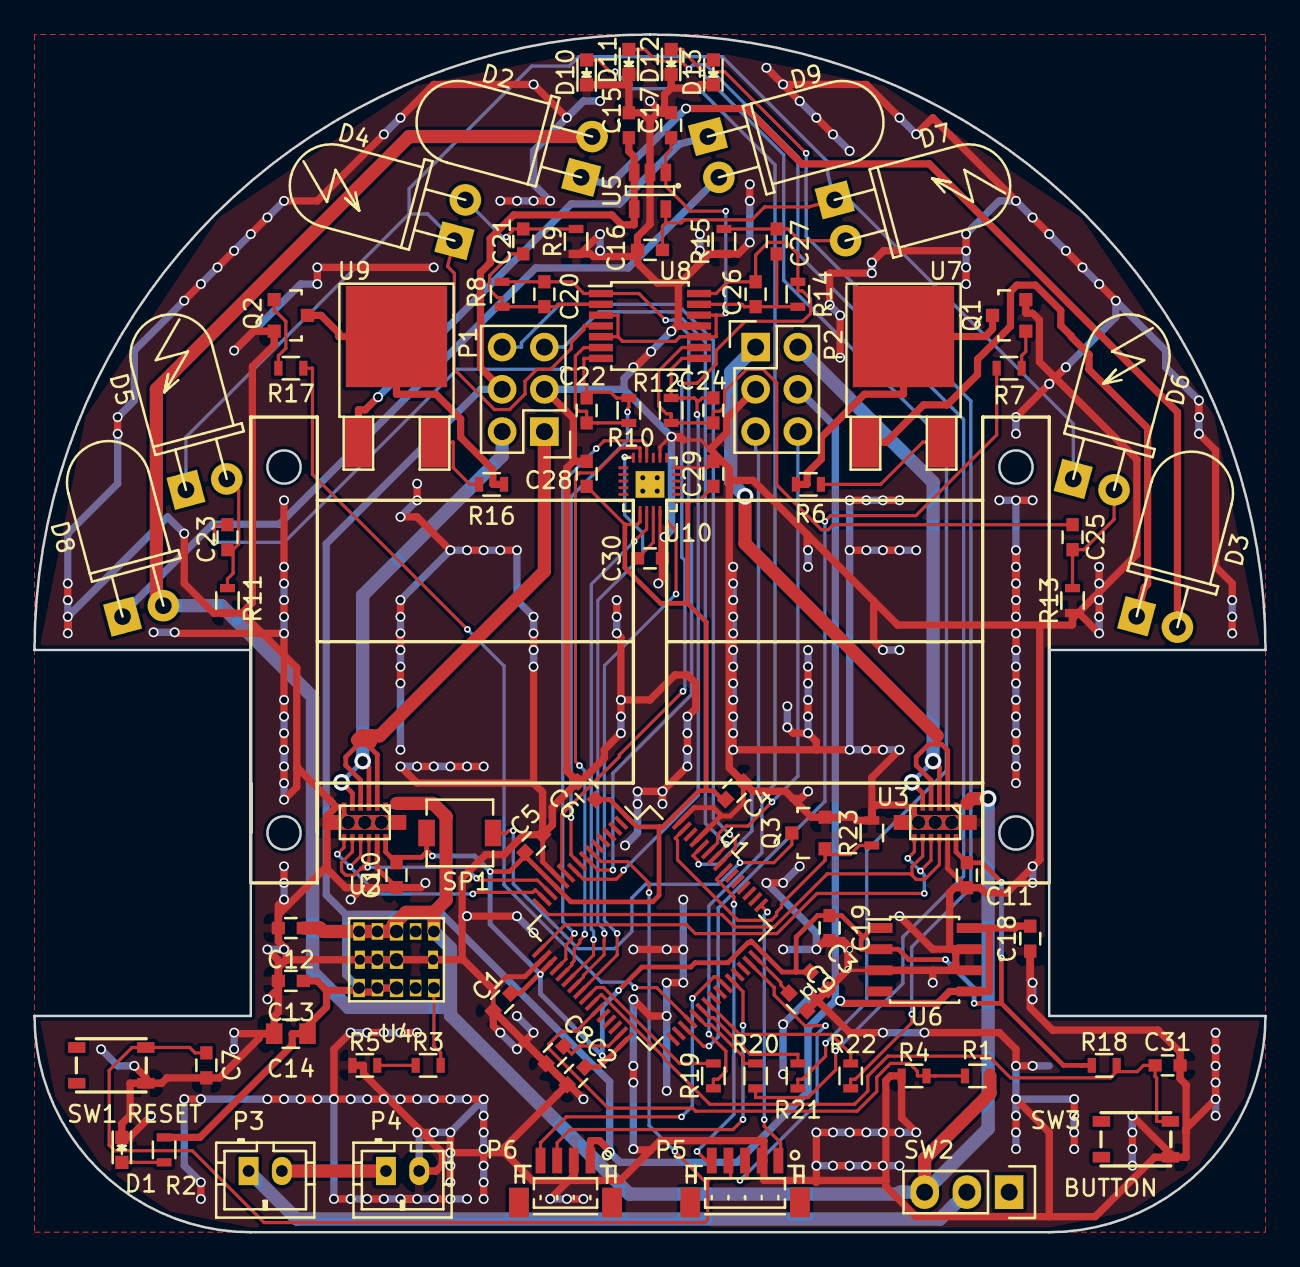
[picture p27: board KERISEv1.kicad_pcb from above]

Board: 2 copper layers, 74.0 x 72.0 mm, 90 parts (0 on the bottom side), 73 nets.

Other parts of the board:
U4: LXDC55FAAA-203

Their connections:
+5V: U4.7, U4.8, U4.9; also elsewhere on the board
+BATT: U4.1, U4.3, U4.4, U4.5; also elsewhere on the board
GND: U4.6, U4.12, U4.13, U4.14; also elsewhere on the board
unnamed 57: U4.11; also elsewhere on the board

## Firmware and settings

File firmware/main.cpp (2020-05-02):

/*
 * main.cpp
 *
 *  Created on: 2016/10/23
 *      Author: kerikun11
 */

#include "mbed.h"
#include "rtos.h"

#include "config.h"
#include "Battery.h"
#include "Buzzer.h"
#include "Button.h"
#include "Motor.h"
#include "Encoder.h"
#include "MPU6500.h"
#include "Reflector.h"
#include "WallDetector.h"
#include "SpeedController.h"
#include "MoveAction.h"
#include "MazeSolver.h"

/* define each pointer */
BusOut *led;
Battery *bat;
Buzzer *bz;
Button *btn;

Motor *mt;
Encoders *enc;
MPU6500 *mpu;
Reflector *rfl;
WallDetector *wd;

SpeedController *sc;
MoveAction *ma;
MazeSolver *ms;

bool output = false;

void debug_info() {
	while (1) {
		Thread::wait(10);
//		printf("%.3f,%.3f\n", mpu->velocity.y,sc->actual.trans);

//		printf("%.3f\t%.3f\n", mpu->gyro.z * 180 / M_PI, mpu->angle.z * 180 / M_PI);
//		sc->getPosition().print();

//		const int i = 0;
//		if (output) LOG("%.0f,%.0f,%.0f,%.0f,%.0f\n", sc->target.wheel[i] / 10,
//				sc->actual.wheel[i] / 10, sc->Kp * (sc->target.wheel[i] - sc->actual.wheel[i]) / 10,
//				sc->Kp * sc->Ki * (0 - sc->integral.wheel[i]) / 10,
//				sc->Kp * sc->Kd * (0 - sc->differential.wheel[i]) / 10);
//		if (output) LOG("%.0f,%.0f\n", sc->target.wheel[i], sc->actual.wheel[i]);

//		if (output) LOG("%.0f,%.0f\n", sc->target.trans, sc->actual.trans);

//		LOG("%.3f,%.3f\n", mpu->gyro.z, mpu->angle.z);
//		LOG("%.0f,%.0f\n", mpu->accel.y, mpu->velocity.y);
	}
}

void serial_ctrl() {
	while (1) {
		Thread::wait(100);
		int c = getchar();
		if (c == EOF)
			continue;
		printf("%c\n", (char) c);
		switch (c) {
		case 't':
			bz->play(Buzzer::CONFIRM);
			mpu->calibration();
			break;
		case 'g':
			bz->play(Buzzer::CONFIRM);
			mpu->calibration();
			wd->calibration();
			ma->enable();
			break;
		case 'f':
			bz->play(Buzzer::CANCEL);
			ms->terminate();
			break;
		case 's':
			ma->set_action(MoveAction::START_STEP);
			bz->play(Buzzer::SELECT);
			break;
		case 'i':
			ma->set_action(MoveAction::START_INIT);
			bz->play(Buzzer::SELECT);
			break;
		case 'w':
			ma->set_action(MoveAction::GO_STRAIGHT);
			bz->play(Buzzer::SELECT);
			break;
		case 'a':
			ma->set_action(MoveAction::TURN_LEFT_90);
			bz->play(Buzzer::SELECT);
			break;
		case 'd':
			ma->set_action(MoveAction::TURN_RIGHT_90);
			bz->play(Buzzer::SELECT);
			break;
		case 'b':
			ma->set_action(MoveAction::STOP);
			bz->play(Buzzer::SELECT);
			break;
		case 'r':
			ma->set_action(MoveAction::RETURN);
			bz->play(Buzzer::SELECT);
			break;
		case 'u':
			ms->terminate();
			ma->set_action(MoveAction::START_STEP);
			ma->set_action(MoveAction::TURN_RIGHT_90);
			ma->set_action(MoveAction::TURN_RIGHT_90);
			ma->set_action(MoveAction::RETURN);
			ma->set_action(MoveAction::TURN_LEFT_90);
			ma->set_action(MoveAction::TURN_LEFT_90);
			ma->set_action(MoveAction::RETURN);
			ma->set_action(MoveAction::TURN_RIGHT_90);
			ma->set_action(MoveAction::TURN_RIGHT_90);
			ma->set_action(MoveAction::RETURN);
			ma->set_action(MoveAction::TURN_LEFT_90);
			ma->set_action(MoveAction::TURN_LEFT_90);
			ma->set_action(MoveAction::RETURN);
			ma->set_action(MoveAction::TURN_RIGHT_90);
			ma->set_action(MoveAction::TURN_RIGHT_90);
			ma->set_action(MoveAction::RETURN);
			ma->set_action(MoveAction::TURN_LEFT_90);
			ma->set_action(MoveAction::TURN_LEFT_90);
			ma->set_action(MoveAction::RETURN);
			ma->set_action(MoveAction::TURN_RIGHT_90);
			ma->set_action(MoveAction::TURN_RIGHT_90);
			ma->set_action(MoveAction::RETURN);
			ma->set_action(MoveAction::TURN_LEFT_90);
			ma->set_action(MoveAction::TURN_LEFT_90);
			ma->set_action(MoveAction::RETURN);
			ma->set_action(MoveAction::TURN_RIGHT_90);
			ma->set_action(MoveAction::TURN_RIGHT_90);
			ma->set_action(MoveAction::RETURN);
			ma->set_action(MoveAction::TURN_LEFT_90);
			ma->set_action(MoveAction::TURN_LEFT_90);
			ma->set_action(MoveAction::START_INIT);
			bz->play(Buzzer::CONFIRM);
			mpu->calibration();
			wd->calibration();
			ma->enable();
			break;
		case 'm':
			ms->terminate();
			bz->play(Buzzer::CONFIRM);
			mpu->calibration();
			wd->calibration();
			ms->start();
			break;
		case 'p':
			bz->play(Buzzer::SELECT);
			printf("%05u\t%05u\t%05u\t%05u\n", rfl->sl(), rfl->fl(), rfl->fr(), rfl->sr());
			printf("%06.3f\t%06.3f\t%06.3f\t%06.3f\n", wd->wall_difference().side[0], wd->wall_difference().flont[0],
					wd->wall_difference().flont[1], wd->wall_difference().side[1]);
			printf("%s %s %s %s\n", wd->wall().side[0] ? "X" : ".", wd->wall().flont[0] ? "X" : ".",
					wd->wall().flont[1] ? "X" : ".", wd->wall().side[1] ? "X" : ".");
			printf("Position:\t(%06.1f, %06.1f, %06.3f)\n", sc->getPosition().x, sc->getPosition().y,
					sc->getPosition().theta);
			break;
		}
	}
}

void emergencyTask() {
	while (1) {
		Thread::wait(1);
		if (fabs(mpu->accel.y) > 98000 || fabs(mpu->gyro.z) > 12 * M_PI) {
			mt->emergency_stop();
			ms->terminate();
			bz->play(Buzzer::EMERGENCY);
			while (mt->isEmergency()) {
				*led = 0x0A;
				Thread::wait(100);
				*led = 0x05;
				Thread::wait(100);
			}
		}
	}
}

int main() {
	/* make instances */
	led = new BusOut(LED1_PIN, LED2_PIN, LED3_PIN, LED4_PIN);
	bat = new Battery(BATTERY_PIN);
	bz = new Buzzer(BUZZER_PIN);
	btn = new Button(BUTTON_PIN);

	mt = new Motor;

	enc = new Encoders(ENCODER_L_TIMx, ENCODER_R_TIMx);
	mpu = new MPU6500(MPU6500_MOSI_PIN, MPU6500_MISO_PIN,
	MPU6500_SCLK_PIN,
	MPU6500_SSEL_PIN);

	rfl = new Reflector(IR_LED_SL_FR_PIN, IR_LED_SR_FL_PIN);
	wd = new WallDetector(rfl);

	sc = new SpeedController(mt, enc, mpu);
	ma = new MoveAction(bz, mt, enc, mpu, rfl, wd, sc);
	ms = new MazeSolver(bz, mpu, rfl, ma, wd);

	/* boot */
	{
		printf("\nHello World!\n");
		printf("Battery Voltage: %.3f [V]\n", bat->voltage());
		if (!bat->check()) {
			bz->play(Buzzer::LOW_BATTERY);
			printf("Battery Low!\n");
			while (1) {
				Thread::wait(10);
				if (btn->pressed) {
					btn->flags = 0;
					break;
				}
			}
		}
		bz->play(Buzzer::BOOT);
		*led = bat->gage(16);
		Thread::wait(1000);
		*led = 0;
	}

	/* for debug */
	Thread debugInfoThread(PRIORITY_DEBUG_INFO, STACK_SIZE_DEBUG_INFO);
	debugInfoThread.start(debug_info);
	Thread serialCtrlThread(PRIORITY_SERIAL_CTRL, STACK_SIZE_SERIAL_CTRL);
	serialCtrlThread.start(serial_ctrl);
	Thread emergencyThread(PRIORITY_EMERGENCY_STOP, STACK_SIZE_EMERGENCY);
	emergencyThread.start(emergencyTask);

	int mode = 0;
	while (true) {
		Thread::wait(10);
		while (mt->isEmergency()) {
			Thread::wait(10);
			if (btn->pressed) {
				btn->flags = 0;
				bz->play(Buzzer::BOOT);
				mt->emergency_release();
				*led = 0;
				printf("Released Emergency\n");
			}
		}
		while (ma->actions()) {
			Thread::wait(10);
			if (btn->pressed) {
				btn->flags = 0;
				bz->play(Buzzer::CANCEL);
				ms->terminate();
			}
		}
		if (btn->pressed) {
			btn->flags = 0;
			bz->play(Buzzer::CONFIRM);
			while (1) {
				Thread::wait(100);
				mode = enc->position() / 2;
				mode &= 0x7;
				*led = mode;
				if (btn->pressed) {
					btn->flags = 0;
					bz->play(Buzzer::CONFIRM);
					break;
				}
			}
			rfl->enable();
			while (1) {
				Thread::wait(10);
				if (rfl->flont(0) > 400 && rfl->flont(1) > 400) {
					bz->play(Buzzer::CONFIRM);
					Thread::wait(200);
					switch (mode) {
					case 0:
						ms->terminate();
						mpu->calibration();
						wd->calibration();
						bz->play(Buzzer::CONFIRM);
						ms->start();
						break;
					case 1:
						ms->terminate();
						ma->set_action(MoveAction::START_STEP);
						for (int i = 0; i < 4; i++) {
							ma->set_action(MoveAction::TURN_RIGHT_90);
							ma->set_action(MoveAction::TURN_RIGHT_90);
							ma->set_action(MoveAction::RETURN);
							ma->set_action(MoveAction::TURN_LEFT_90);
							ma->set_action(MoveAction::TURN_LEFT_90);
							ma->set_action(MoveAction::RETURN);
						}
						ma->set_action(MoveAction::TURN_RIGHT_90);
						ma->set_action(MoveAction::TURN_RIGHT_90);
						ma->set_action(MoveAction::RETURN);
						ma->set_action(MoveAction::TURN_LEFT_90);
						ma->set_action(MoveAction::TURN_LEFT_90);
						ma->set_action(MoveAction::START_INIT);
						mpu->calibration();
						wd->calibration();
						ma->enable();
						break;
					case 2:
						ma->set_action(FastTrajectory::FAST_GO_HALF);
						ma->set_action(FastTrajectory::FAST_TURN_RIGHT_45);
						ma->set_action(FastTrajectory::FAST_TURN_LEFT_45_45);
						ma->set_action(FastTrajectory::FAST_TURN_RIGHT_45_45);
						ma->set_action(FastTrajectory::FAST_TURN_LEFT_45_45);
						ma->set_action(FastTrajectory::FAST_TURN_RIGHT_45_45);
						ma->set_action(FastTrajectory::FAST_TURN_LEFT_135R);
						ma->set_action(FastTrajectory::FAST_TURN_LEFT_90);
						for (int i = 0; i < 4; i++) {
							ma->set_action(FastTrajectory::FAST_GO_HALF);
							ma->set_action(FastTrajectory::FAST_TURN_LEFT_45);
							ma->set_action(FastTrajectory::FAST_TURN_RIGHT_45_45);
							ma->set_action(FastTrajectory::FAST_TURN_LEFT_45_45);
							ma->set_action(FastTrajectory::FAST_TURN_RIGHT_45_45);
							ma->set_action(FastTrajectory::FAST_TURN_LEFT_135R);
							ma->set_action(FastTrajectory::FAST_TURN_LEFT_90);
						}
						ma->set_action(FastTrajectory::FAST_GO_HALF);
						ma->set_action(FastTrajectory::FAST_TURN_LEFT_45);
						ma->set_action(FastTrajectory::FAST_TURN_RIGHT_45_45);
						ma->set_action(FastTrajectory::FAST_TURN_LEFT_45_45);
						ma->set_action(FastTrajectory::FAST_TURN_RIGHT_45_45);
						ma->set_action(FastTrajectory::FAST_TURN_LEFT_45R);
						ma->set_action(FastTrajectory::FAST_GO_HALF);
						mpu->calibration();
						wd->calibration();
						ma->enable();
						break;
					case 3:
						for (int i = 0; i < 4; i++) {
							ma->set_action(FastTrajectory::FAST_GO_STRAIGHT);
							ma->set_action(FastTrajectory::FAST_GO_STRAIGHT);
							ma->set_action(FastTrajectory::FAST_TURN_RIGHT_90);
							ma->set_action(FastTrajectory::FAST_TURN_RIGHT_90);
							ma->set_action(FastTrajectory::FAST_GO_STRAIGHT);
							ma->set_action(FastTrajectory::FAST_GO_STRAIGHT);
							ma->set_action(FastTrajectory::FAST_TURN_RIGHT_90);
							ma->set_action(FastTrajectory::FAST_TURN_RIGHT_90);
						}
						mpu->calibration();
						wd->calibration();
						ma->enable();
						break;
					case 4:
						ma->set_action(FastTrajectory::FAST_TURN_RIGHT_90);
						for (int i = 0; i < 4; i++) {
							ma->set_action(FastTrajectory::FAST_TURN_LEFT_90);
							ma->set_action(FastTrajectory::FAST_TURN_LEFT_90);
							ma->set_action(FastTrajectory::FAST_TURN_LEFT_90);
							ma->set_action(FastTrajectory::FAST_TURN_LEFT_90);
							ma->set_action(FastTrajectory::FAST_TURN_RIGHT_90);
							ma->set_action(FastTrajectory::FAST_TURN_RIGHT_90);
							ma->set_action(FastTrajectory::FAST_TURN_RIGHT_90);
							ma->set_action(FastTrajectory::FAST_TURN_RIGHT_90);
						}
						ma->set_action(FastTrajectory::FAST_TURN_LEFT_90);
						mpu->calibration();
						wd->calibration();
						ma->enable();
						break;
					case 5:
						for (int i = 0; i < 4; i++) {
							ma->set_action(FastTrajectory::FAST_GO_STRAIGHT);
							ma->set_action(FastTrajectory::FAST_GO_STRAIGHT);
							ma->set_action(FastTrajectory::FAST_TURN_RIGHT_180);
							ma->set_action(FastTrajectory::FAST_GO_STRAIGHT);
							ma->set_action(FastTrajectory::FAST_GO_STRAIGHT);
							ma->set_action(FastTrajectory::FAST_TURN_RIGHT_180);
						}
						mpu->calibration();
						wd->calibration();
						ma->enable();
						break;
					}
					break;
				}
				if (btn->pressed) {
					btn->flags = 0;
					bz->play(Buzzer::CANCEL);
					ms->terminate();
					rfl->disable();
					break;
				}
			}
		}
	}
}

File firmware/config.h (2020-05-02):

/*
 * config.h
 *
 *  Created on: 2016/10/23
 *      Author: kerikun11
 */

#ifndef CONFIG_H_
#define CONFIG_H_

#include "mbed.h"

/* Thread Priorities */

#define PRIORITY_REFLECTOR_UPDATE	osPriorityHigh
#define PRIORITY_MPU6500_UPDATE		osPriorityHigh

#define PRIORITY_WALL_UPDATE		osPriorityAboveNormal
#define PRIORITY_ENCODER_UPDATE		osPriorityAboveNormal

#define PRIORITY_EMERGENCY_STOP		osPriorityAboveNormal
#define PRIORITY_SPEED_CONTROLLER	osPriorityAboveNormal

#define PRIORITY_MOVE_ACTION		osPriorityNormal
#define PRIORITY_BUZZER				osPriorityNormal

#define PRIORITY_MAZE_SOLVER		osPriorityBelowNormal

#define PRIORITY_DEBUG_INFO			osPriorityLow

#define PRIORITY_SERIAL_CTRL		osPriorityIdle

/* thread stack size */

#define STACK_SIZE_BUZZER			1024
#define STACK_SIZE_ENCODER			512
#define STACK_SIZE_MAZE_SOLVER		4096
#define STACK_SIZE_MOVE_ACTION		2048
#define STACK_SIZE_MPU6500_UPDATE	1024
#define STACK_SIZE_REFLECTOR_UPDATE	512
#define STACK_SIZE_SPEED_CONTROLLER	1024
#define STACK_SIZE_WALL_UPDATE		512
#define STACK_SIZE_DEBUG_INFO		2048
#define STACK_SIZE_SERIAL_CTRL		2048
#define STACK_SIZE_EMERGENCY		512

/* Hardware Parameter */

#define MACHINE_ROTATION_RADIUS		21.0f	// [mm]
#define WHEEL_DIAMETER_MM			24.65f
#define WHEEL_GEER_RATIO			0.25f
#define ENCODER_PULSES				(1024*4)

/* Calibration Parameter */

#define WALL_DETECTOR_FLONT_RATIO	1.82f	/* KERISEv1 */
//#define WALL_DETECTOR_FLONT_RATIO	1.33f	/* KERISEv2 */

#define MPU6500_UPDATE_PERIOD_US	1000

/* Pin Mapping */

#define BATTERY_PIN			PB_1

#define BUZZER_PIN			PB_9	//< Modify PeripheralPins.c PWM Pin using Timer11	KERISEv1
//#define BUZZER_PIN			PB_8	//< Modify PeripheralPins.c PWM Pin using Timer10	KERISEv2

#define BUTTON_PIN			PB_0

#define LED1_PIN			PC_5
#define LED2_PIN			PC_6
#define LED3_PIN			PC_7
#define LED4_PIN			PC_8

#define MPU6500_MOSI_PIN	PA_7
#define MPU6500_MISO_PIN	PA_6
#define MPU6500_SCLK_PIN	PA_5
#define MPU6500_SSEL_PIN	PA_4

#define IR_LED_SL_FR_PIN	PB_14
#define IR_LED_SR_FL_PIN	PB_15

#define MOTOR_TIMx						TIM2
#define MOTOR_TIMx_CLK_ENABLE()			__HAL_RCC_TIM2_CLK_ENABLE()
#define MOTOR_TIMx_CHANNEL_GPIO_PORT()	do{__HAL_RCC_GPIOA_CLK_ENABLE();}while(0)
#define MOTOR_TIMx_GPIO_PORT_CHANNEL1	GPIOA
#define MOTOR_TIMx_GPIO_PORT_CHANNEL2	GPIOA
#define MOTOR_TIMx_GPIO_PORT_CHANNEL3	GPIOA
#define MOTOR_TIMx_GPIO_PORT_CHANNEL4	GPIOA
#define MOTOR_TIMx_GPIO_PIN_CHANNEL1	GPIO_PIN_0
#define MOTOR_TIMx_GPIO_PIN_CHANNEL2	GPIO_PIN_1
#define MOTOR_TIMx_GPIO_PIN_CHANNEL3	GPIO_PIN_2
#define MOTOR_TIMx_GPIO_PIN_CHANNEL4	GPIO_PIN_3
#define MOTOR_TIMx_GPIO_AF_CHANNEL		GPIO_AF1_TIM2

/* Definition for ADCx clock resources */
#define ADCx_S							ADC2
#define ADCx_F							ADC3
#define ADCx_S_CLK_ENABLE()				__HAL_RCC_ADC2_CLK_ENABLE()
#define ADCx_F_CLK_ENABLE()				__HAL_RCC_ADC3_CLK_ENABLE()
#define ADCx_CHANNEL_GPIO_CLK_ENABLE()  __HAL_RCC_GPIOC_CLK_ENABLE()

#define ADCx_FORCE_RESET()              __HAL_RCC_ADC_FORCE_RESET()
#define ADCx_RELEASE_RESET()            __HAL_RCC_ADC_RELEASE_RESET()

/* Definition for ADCx Channel Pin */
#define ADCx_CHANNEL_SL_PIN             GPIO_PIN_0
#define ADCx_CHANNEL_FL_PIN             GPIO_PIN_1
#define ADCx_CHANNEL_FR_PIN             GPIO_PIN_2
#define ADCx_CHANNEL_SR_PIN             GPIO_PIN_3
#define ADCx_CHANNEL_GPIO_PORT          GPIOC

/* Definition for ADCx's Channel */
#define ADCx_CHANNEL_SL					ADC_CHANNEL_10
#define ADCx_CHANNEL_FL					ADC_CHANNEL_11
#define ADCx_CHANNEL_FR					ADC_CHANNEL_12
#define ADCx_CHANNEL_SR					ADC_CHANNEL_13

/*
 * TIM1		IR LED
 * TIM2		mbed timer
 * TIM3		Encoder L
 * TIM4		Encoder R
 * TIM5		*
 * TIM6
 * TIM7
 * TIM8
 * TIM9
 * TIM10
 * TIM11
 * TIM12
 * TIM13
 * TIM14
 */

/*
 * PA0	Motor IN1 L		TIM2_CH1				HAL
 * PA1	Motor IN2 L		TIM2_CH2				HAL
 * PA2	UART TX			UART2_TX				mbed
 * PA2	UART RX			UART2_RX				mbed
 * PA4	MPU6500 nCS		SPI1_NSS				mbed
 * PA5	MPU6500 SCK		SPI1_SCK				mbed
 * PA6	MPU6500 nMISO	SPI1_MISO				mbed
 * PA7	MPU6500 MOSI	SPI1_MOSI				mbed
 * PA8	NC
 * PA9
 * PA10
 * PA11	NC
 * PA12	NC
 * PA13	ST-Link SWDIO	SWDIO
 * PA14	ST-Link SWCLK	SWCLK
 * PA15	NC
 *
 * PB0	Button									mbed
 * PB1	Battery Voltage	ADC1_IN8 / ADC2_IN8		mbed
 * PB2	NC
 * PB3	ST-Link SWO		SWO
 * PB4	Encoder L A		TIM3_CH1				HAL
 * PB5	Encoder L B		TIM3_CH2				HAL
 * PB6	Encoder R A		TIM4_CH1				HAL
 * PB7	Encoder R B		TIM4_CH2				HAL
 * PB8	Speaker			TIM10_CH1				mbed (change mbed timer)
 * PB9	Motor IN1 R		TIM2_CH3				HAL
 * PB10	Motor IN2 R		TIM2_CH4				HAL
 * PB11	NC
 * PB12	NC
 * PB13	NC
 * PB14	IR LED SL FR	TIM1_CH2N				mbed
 * PB15	IR LED SL FR	TIM1_CH3N				mbed
 *
 * PC0	IR Receiver SL	ADC1_IN10				HAL
 * PC1	IR Receiver FL	ADC1_IN11				HAL
 * PC2	IR Receiver FR	ADC1_IN12				HAL
 * PC3	IR Receiver SR	ADC1_IN13				HAL
 * PC4	MPU6500 Int
 * PC5	LED1
 * PC6	LED2
 * PC7	LED3
 * PC8	LED4
 * PC9	NC
 * PC10	NC
 * PC11	NC
 * PC12	NC
 * PC13	NC
 * PC14	NC
 * PC15	NC
 */

#endif /* CONFIG_H_ */

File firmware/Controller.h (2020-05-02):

/*
 * Controller.h
 *
 *  Created on: 2016/10/28
 *      Author: kerikun11
 */

#ifndef CONTROLLER_H_
#define CONTROLLER_H_

#include "mbed.h"
#include "config.h"

#define SPEED_CONTROLLER_PERIOD_US	500

class Position {
public:
	Position(float x = 0, float y = 0, float theta = 0) :
			x(x), y(y), theta(theta) {
	}
	float x, y, theta;
	void reset() {
		x = 0;
		y = 0;
		theta = 0;
	}
	void set(float x = 0, float y = 0, float theta = 0) {
		this->x = x;
		this->y = y;
		this->theta = theta;
	}
	Position rotate(float angle) {
		return Position(x * cos(angle) - y * sin(angle), x * sin(angle) + y * cos(angle),
				theta + angle);
	}
	Position operator=(const Position &obj) {
		x = obj.x;
		y = obj.y;
		theta = obj.theta;
		return *this;
	}
	Position operator-(const Position &obj) const {
		return Position(x - obj.x, y - obj.y, theta - obj.theta);
	}
	Position operator+(const Position &obj) const {
		return Position(x + obj.x, y + obj.y, theta + obj.theta);
	}
	Position operator/(const float &div) {
		return Position(x / div, y / div, theta / div);
	}
	Position operator-() const {
		return Position(-x, -y, -theta);
	}
	Position operator+() const {
		return Position(x, y, theta);
	}
};

class WheelParameter {
public:
	WheelParameter(float trans = 0, float rot = 0) :
			trans(trans), rot(rot) {
	}
	float trans;	//< translation
	float rot;		//< rotation
	float wheel[2];	//< wheel [0]: left, [1]: right
	void pole2wheel() {
		wheel[0] = trans - MACHINE_ROTATION_RADIUS * rot;
		wheel[1] = trans + MACHINE_ROTATION_RADIUS * rot;
	}
	void wheel2pole() {
		rot = (wheel[1] - wheel[0]) / 2.0f / MACHINE_ROTATION_RADIUS;
		trans = (wheel[1] + wheel[0]) / 2.0f;
	}
};

class SpeedController {
public:
	SpeedController(Motor *mt, Encoders *enc, MPU6500 *mpu) :
			mt(mt), enc(enc), mpu(mpu), ctrlThread(PRIORITY_SPEED_CONTROLLER) {
		ctrlThread.start(this, &SpeedController::ctrlTask);
		for (int i = 0; i < 2; i++) {
			target_p.wheel[i] = 0;
			for (int j = 0; j < 3; j++) {
				wheel_position[j][i] = 0;
			}
			actual_p.wheel[i] = 0;
			actual_i.wheel[i] = 0;
			actual_d.wheel[i] = 0;
		}
	}
	void enable() {
		ctrlTicker.attach_us(this, &SpeedController::ctrlIsr,
		SPEED_CONTROLLER_PERIOD_US);
	}
	void disable() {
		ctrlTicker.detach();
	}
	void set_target(float trans, float rot) {
		target_p.trans = trans;
		target_p.rot = rot;
		target_p.pole2wheel();
	}
	WheelParameter& actual() {
		return actual_p;
	}
	Position position;
private:
	Motor *mt;
	Encoders *enc;
	MPU6500 *mpu;
	Thread ctrlThread;
	Ticker ctrlTicker;
	float wheel_position[3][2];
	WheelParameter target_p;
	WheelParameter actual_p;
	WheelParameter actual_i;
	WheelParameter actual_d;

	void ctrlIsr() {
		ctrlThread.signal_set(0x01);
	}
	void ctrlTask() {
		while (1) {
			Thread::signal_wait(0x01);
			for (int i = 0; i < 2; i++) {
				wheel_position[2][i] = wheel_position[1][i];
				wheel_position[1][i] = wheel_position[0][i];
				wheel_position[0][i] = enc->position(i);
			}
			for (int i = 0; i < 2; i++) {
				actual_p.wheel[i] = (wheel_position[0][i] - wheel_position[1][i])
						* 1000000/ SPEED_CONTROLLER_PERIOD_US;
				actual_i.wheel[i] += (actual_p.wheel[i] - target_p.wheel[i])
						* SPEED_CONTROLLER_PERIOD_US / 1000000;
				if (actual_i.wheel[i] > 10) actual_i.wheel[i] = 10;
				if (actual_i.wheel[i] < -10) actual_i.wheel[i] = -10;
				actual_d.wheel[i] = (wheel_position[0][i] - 2 * wheel_position[1][i]
						+ wheel_position[2][i]) * 1000000 / SPEED_CONTROLLER_PERIOD_US;
			}
			actual_p.wheel2pole();
			actual_p.rot = mpu->gyroZ() * M_PI / 180.0f;
			actual_p.pole2wheel();
			const float Kp = 1;
			const float Ki = 0.1;
			const float Kd = 0.2;
			float pwm_value[2];
			for (int i = 0; i < 2; i++) {
				pwm_value[i] = Kp * (target_p.wheel[i] - actual_p.wheel[i])
						+ Ki * (0 - actual_i.wheel[i]) + Kd * (0 - actual_d.wheel[i]);
			}
			mt->drive(pwm_value[0], pwm_value[1]);

			position.theta += actual_p.rot * SPEED_CONTROLLER_PERIOD_US / 1000000;
			position.x += actual_p.trans * cos(position.theta) * SPEED_CONTROLLER_PERIOD_US
					/ 1000000;
			position.y += actual_p.trans * sin(position.theta) * SPEED_CONTROLLER_PERIOD_US
					/ 1000000;
		}
	}
};

class MoveAction {
public:
	MoveAction(Buzzer *bz, Encoders *enc, MPU6500 *mpu, Reflector *rfl, WallDetector *wd,
			SpeedController *sc) :
			bz(bz), enc(enc), mpu(mpu), rfl(rfl), wd(wd), sc(sc), thread(PRIORITY_MOVE_ACTION) {
		_actions = 0;
	}
	enum ACTION {
		START_STEP,
		START_INIT,
		GO_STRAIGHT,
		TURN_LEFT_90,
		TURN_RIGHT_90,
		RETURN,
		FAST_START_STEP,
		FAST_GO_STRAIGHT,
		FAST_GO_DIAGONAL,
		FAST_TURN_LEFT_45,
		FAST_TURN_LEFT_90,
		FAST_TURN_RIGHT_45,
		FAST_TURN_RIGHT_90,
		FAST_STOP,
	};
	const char* action_string(enum ACTION action) {
		static const char name[][32] = { "start_step", "start_init", "go_straight", "turn_left_90",
				"turn_right_90", "return", "fast_start_step", "fast_go_straight",
				"fast_go_diagonal", "fast_turn_left_45", "fast_turn_left_90", "fast_turn_right_45",
				"fast_turn_right_90", "fast_stop" };
		return name[action];
	}
	void enable() {
		error.reset();
		sc->position = error;
		if (actions() == 0) {
			rfl->enable();
			sc->enable();
			thread.start(this, &MoveAction::task);
		}
	}
	void disable() {
		thread.terminate();
		sc->disable();
		rfl->disable();
		while (1) {
			osEvent evt = queue.get(0);
			if (evt.status != osEventMessage) {
				break;
			}
		}
		_actions = 0;
	}
	void set_action(enum ACTION action) {
		_actions++;
		queue.put((enum ACTION*) action);
	}
	int actions() const {
		return _actions;
	}
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

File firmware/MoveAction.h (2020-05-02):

/*
 * MoveAction.h
 *
 *  Created on: 2016/11/11
 *      Author: kerikun11
 */

#ifndef MOVEACTION_H_
#define MOVEACTION_H_

#include "mbed.h"
#include "config.h"
#include <vector>
#include <queue>

#define MOVE_ACTION_PERIOD			1000
#define WALL_ATTACH_ENABLED			false
#define WALL_AVOID_ENABLED			false

//#define LOOK_AHEAD_UNIT				10
//#define DETERMINE_VELOCITY_UNIT		10
#define TRAJECTORY_PROP_GAIN		100
#define TRAJECTORY_INT_GAIN			10

class Trajectory {
public:
	Trajectory(bool accel = false) :
			accel(accel) {
		reset();
	}
	virtual ~Trajectory() {
	}
	void reset() {
		last_index = 0;
	}
	Position getNextDir(const Position &cur, float velocity) {
		int index_cur = getNextIndex(cur);
		if (accel) {
//			float t1 = getPosition(index_cur + 0).theta;
//			float t2 = getPosition(index_cur + 20).theta;
//			float t3 = getPosition(index_cur + 40).theta;
//			float t4 = getPosition(index_cur + 60).theta;
//			float theta = fabs(t1 - t2) * 3 + fabs(t2 - t3) * 2 + fabs(t3 - t4);
//			velocity *= 1 / (1 + theta / 6);
		}
		int look_ahead = 60;
		Position dir = (getPosition(index_cur + look_ahead) - cur).rotate(-cur.theta);
		dir.theta = atan2f(dir.y, dir.x);
		dir *= velocity / look_ahead;
		return dir;
	}
	float getRemain() const {
		return (getSize() - last_index) * interval;
	}
	Position getEndPosition() {
		return getPosition(getSize());
	}
protected:
	int last_index;
	const float interval = 1.0f;
	bool accel;
	virtual int size() const {
		return 180;
	}
	virtual Position position(int index) const {
		return Position(index * interval, 0, 0);
	}
	virtual void cache(int index) {
	}
	int getSize() const {
		return size();
	}
	Position getPosition(const int index) {
		return position(index);
	}
	int getNextIndex(const Position& pos) {
		for (int i = last_index;; i++) {
			Position target = getPosition(i);
			Position dir = (target - pos).rotate(-target.theta);
			if (dir.x > 0) {
				last_index = i;
				cache(last_index);
				return last_index;
			}
		}
		return last_index;
	}
};

class FastTrajectory: public Trajectory {
public:
	enum FAST_ACTION {
		FAST_GO_STRAIGHT,
		FAST_GO_HALF,
		FAST_GO_DIAGONAL,
		FAST_TURN_LEFT_45,
		FAST_TURN_RIGHT_45,
		FAST_TURN_LEFT_45R,
		FAST_TURN_RIGHT_45R,
		FAST_TURN_LEFT_45_45,
		FAST_TURN_RIGHT_45_45,
		FAST_TURN_LEFT_45_S_45,
		FAST_TURN_RIGHT_45_S_45,
		FAST_TURN_LEFT_90,
		FAST_TURN_RIGHT_90,
		FAST_TURN_LEFT_135,
		FAST_TURN_RIGHT_135,
		FAST_TURN_LEFT_135R,
		FAST_TURN_RIGHT_135R,
		FAST_TURN_LEFT_180,
		FAST_TURN_RIGHT_180,
	};
	FastTrajectory(std::vector<enum FAST_ACTION> actions) :
			Trajectory(true), actions(actions) {
		point_index = 0;
		action_index = 0;
		cached_action_index = 0;
		cached_index = 0;
		sum = 0;
		for (int i = 0; i < (int) actions.size(); i++) {
			sum += point_size(actions[i]);
		}

//		for (int i = 0; i < (int) actions.size(); i++)
//			printf("%d, ", actions[i]);
//		printf("size:%d\n", size());
//		for (int i = 0; i < size() + 360; i++) {
//			Thread::wait(10);
//			printf("%f,%f,%f\n", position(i).x, position(i).y, position(i).theta);
//			cache(i);
//		}
	}
private:
	int point_index;
	int action_index;
	int cached_index;
	int cached_action_index;
	int sum;
	Position cached_position;
	std::vector<enum FAST_ACTION> actions;
	virtual int size() const {
		return sum;
	}
	virtual Position position(int index) const {
		Position ret = cached_position;
		index -= cached_index;
		for (int i = cached_action_index; i < (int) actions.size(); i++) {
			FAST_ACTION act = actions[i];
			if (index < point_size(act)) {
				ret += point(actions[i], index).rotate(ret.theta);
				return ret;
			}
			index -= point_size(act);
			ret += point(act, point_size(act)).rotate(ret.theta);
		}
		ret += point(FAST_GO_STRAIGHT, index).rotate(ret.theta);
		return ret;
	}
	virtual void cache(int index) {
		if (cached_action_index < (int) actions.size()) {
			FAST_ACTION act = actions[cached_action_index];
			if (index > cached_index + point_size(act)) {
				cached_position += point(act, point_size(act)).rotate(cached_position.theta);
				cached_index += point_size(act);
				cached_action_index++;
				printf("#: %d\n", cached_action_index);
			}
		}
	}
	int point_size(const enum FAST_ACTION action) const {
		switch (action) {
		case FAST_GO_STRAIGHT:
			return 180;
		case FAST_GO_HALF:
			return 90;
		case FAST_GO_DIAGONAL:
			return 90.0f * 1.41421356f / 2;
		case FAST_TURN_LEFT_45:
		case FAST_TURN_RIGHT_45:
		case FAST_TURN_LEFT_45R:
		case FAST_TURN_RIGHT_45R:
			return 211;
		case FAST_TURN_LEFT_45_45:
		case FAST_TURN_RIGHT_45_45:
			return 214;
		case FAST_TURN_LEFT_45_S_45:
		case FAST_TURN_RIGHT_45_S_45:
			return 428;
		case FAST_TURN_LEFT_90:
		case FAST_TURN_RIGHT_90:
			return 151;
		case FAST_TURN_LEFT_135:
		case FAST_TURN_RIGHT_135:
		case FAST_TURN_LEFT_135R:
		case FAST_TURN_RIGHT_135R:
			return 278;
		case FAST_TURN_LEFT_180:
		case FAST_TURN_RIGHT_180:
			return 459;
		default:
			return 180;
		}
	}
	Position point(const enum FAST_ACTION action, const int index) const {
		static const float data_45[211 + 1][3] = {
				{ 0, 0, 0 },
				{ 1.0053, 1.0686e-10, 1.0686e-08 },
				{ 2.0053, 1.8899e-05, 5.5045e-05 },
				{ 3.0053, 0.0001468, 0.00021694 },
				{ 4.0053, 0.00049056, 0.0004857 },
				{ 5.0053, 0.001157, 0.00086132 },
				{ 6.0053, 0.0022531, 0.0013438 },
				{ 7.0053, 0.0038856, 0.0019331 },
				{ 8.0053, 0.0061615, 0.0026294 },
				{ 9.0053, 0.0091875, 0.0034324 },
				{ 10.005, 0.01307, 0.0043424 },
				{ 11.005, 0.017917, 0.0053592 },
				{ 12.005, 0.023835, 0.0064828 },
				{ 13.005, 0.03093, 0.0077133 },
				{ 14.005, 0.03931, 0.0090507 },
				{ 15.005, 0.049081, 0.010495 },
				{ 16.005, 0.06035, 0.012046 },
				{ 17.005, 0.073224, 0.013704 },
				{ 18.005, 0.08781, 0.015469 },
				{ 19.005, 0.10421, 0.017341 },
				{ 20.005, 0.12254, 0.019319 },
				{ 21.004, 0.14291, 0.021405 },
				{ 22.004, 0.16541, 0.023597 },
				{ 23.004, 0.19015, 0.025896 },
				{ 24.003, 0.21725, 0.028302 },
				{ 25.003, 0.24681, 0.030815 },
				{ 26.002, 0.27893, 0.033435 },
				{ 27.002, 0.31373, 0.036161 },
				{ 28.001, 0.3513, 0.038995 },
				{ 29, 0.39176, 0.041935 },
				{ 29.999, 0.43521, 0.044982 },
				{ 30.998, 0.48176, 0.048136 },
				{ 31.997, 0.53152, 0.051397 },
				{ 32.996, 0.58458, 0.054765 },
				{ 33.994, 0.64106, 0.058239 },
				{ 34.992, 0.70106, 0.061821 },
				{ 35.99, 0.76469, 0.065509 },
				{ 36.988, 0.83206, 0.069304 },
				{ 37.985, 0.90327, 0.073207 },
				{ 38.983, 0.97842, 0.077215 },
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
		static const float data_45_r[211 + 1][3] = {
				{ 0, 0, 0 },
				{ 1, 0, 0 },
				{ 2, 0, 0 },
				{ 3, 0, 0 },
				{ 4, 0, 0 },
				{ 5, 0, 0 },
				{ 6, 0, 0 },
				{ 7, 0, 0 },
				{ 8, 0, 0 },
				{ 9, 0, 0 },
				{ 10, 0, 0 },
				{ 11, 0, 0 },
				{ 12, 0, 0 },
				{ 13, 0, 0 },
				{ 14, 0, 0 },
				{ 15, 0, 0 },
				{ 16, 0, 0 },
				{ 17, 0, 0 },
				{ 18, 0, 0 },
				{ 19, 0, 0 },
				{ 20, 0, 0 },
				{ 21, 0, 0 },
				{ 22, 0, 0 },
				{ 23, 0, 0 },
				{ 24, 0, 0 },
				{ 25, 0, 0 },
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

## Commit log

2016-09-09 add kicad files
    [6AXIS_SENSOR.sch, AXIS_SENSOR.sch, COM.sch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]
2016-09-09 ベタグランドの修正
    モータードライバの放熱効果を高めるために，サーマルリリーフをやめてベタ接続に．
    [Mouse-01-B.Cu.gbl, Mouse-01-B.Mask.gbs, Mouse-01-B.SilkS.gbo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]
2016-09-12 基板発注済ガーバーデータ
    1回目の基板発注
2016-09-12 MATLAB制御講習
    講習時のMATLAB
2016-09-12 Datasheets
    使用部品のデータシートと関連リンク
2020-05-02 mbedファームを追加
    mbed-cli環境
2020-05-02 環境を再構築
    Makefileを追加．
2020-05-02 Batteryチェックプログラムを実装
    起動時にチェック
2020-05-02 モーター駆動プログラムを実装
    1kHzなのでうるさい．．．
2020-05-02 ジャイロとインターフェース
2020-05-02 モーター
2020-05-02 ブザーとボタンを独立化
2020-05-02 リフレクタの駆動プログラムの実装
    FFTはまだ．
    [_saved_Mouse-01.sch]
2020-05-02 フォトリフレクタのFFTを実装，ブザーをOS化
2020-05-02 インスタンスはmain関数の最初で生成，BuzzerのRTOSを改良
2020-05-02 エンコーダを初期化
    newのせいで不定値になっていたのを修正
2020-05-02 部品表の追加
    xmlとcsv
    [Mouse-01.csv]
2020-05-02 マウンタとホイールの3Dデータ
    20160917にDMM.makeに発注したデータ
    [2set.stl]
2020-05-02 3D-CADデータの更新
    [both-2set.stl, mounter-8set.stl, wheel-2set.stl]
2020-05-02 フットプリントを追加
2020-05-02 バッテリーのデータシート
2020-05-02 CADデータの更新
    [mounter-4set.stl]
2020-05-02 シリアルによるラジコン
2020-05-02 エンコーダによる並進位置のPID制御
    [_saved_Mouse-01.sch]
2020-05-02 フォトリフレクタのFFTを廃止，強さだけを読む
2020-05-02 壁と平行に走行
    壁があるかも判定し，ある場合は平行に走行
2020-05-02 前の壁を認識して垂直に止まる
2020-05-02 カエルの歌を実装...
2020-05-02 マスの移動プログラムを実装
    壁を見ながら
2020-05-02 パラメータの調整，緊急停止
2020-05-02 間欠データアップデート処理のRTOS化
2020-05-02 外形の寸法の表示の修正
    76 mm => 74 mm
    [Mouse-01.kicad_pcb]
2020-05-02 速度制御器の実装
    エンコーダーのデータををもとにモーターを目標速度で走行させる．PIDパラメータはまだ．
2020-05-02 区画の走行を安定化
    壁を利用
2020-05-02 EncoderMeasureとGyroMeasureは使わないので削除
2020-05-02 RETURNアクションを追加
    転回して，4cm前へ進む．
2020-05-02 移動不可能な方向にはエラーを出す
2020-05-02 停止位置の変更
    次のマスに頭を突っ込んだ状態から，完全に入った状態に変更
2020-05-02 MazeSolverを追加
    井土さんより頂いたプログラム
2020-05-02 周波数成分抽出プログラムを追加
    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
2020-05-02 MazeSolverのcppファイルをMakefileに追加
2020-05-02 優先順位を整理
2020-05-02 sqrtの中身が負になるバグを修正
2020-05-02 カーブは等速円運動
    とりあえず動く
2020-05-02 カーブはせずに，直進・回転・直進で曲がる
2020-05-02 MoveActionに開始と停止のスイッチを実装
2020-05-02 MazeSolverのインタフェースを作成
    まだ途中
2020-05-02 迷路のテスト走行
2020-05-02 停止位置は，x=60mm
2020-05-02 安定性の向上
2020-05-02 パラメータの調整
2020-05-02 区画の移動を座標で管理，誤差を次につなげる
2020-05-02 wall_avoidを座標変更へ
    角速度を変更するのではなく，y座標を調整する．
2020-05-02 MPUのレジスタマップを追加
2020-05-02 クラスとファイルの置き場所を調整
2020-05-02 クラスとファイルの置き場所の更新2
2020-05-02 迷路探索と最速走行の動作を切り分けて別々にアクセス
2020-05-02 アクションを選択するUIを作成
    エンコーダを利用
2020-05-02 インターフェースの調整
2020-05-02 スピード選択を実装，リセットせずに続けて走行
2020-05-02 折り返すときに，通し角度の絶対値が大きくならない方向へ曲がる
2020-05-02 最速走行が終了したら，スタートへ戻り，スピードを上げて再チャレ
    未動作検証．
2020-05-02 ログを見ながらPIDパラメータを調整
    実はI要素がほとんど働いていなかったことがわかった．
2020-05-02 コメントを調整
2020-05-02 とりあえずスラローム
    フィードフォワード&早すぎで全然動かない．
2020-05-02 理科大迷路攻略
    10x10で探索途中でOperator new out of memory
2020-05-02 400mm/sのスラロームを実装
    MATLABでクロソイド曲線の点列を作成し，それに追従する．
    実機確認済．
2020-05-02 各スレッドのスタックサイズを定義
2020-05-02 スラロームを高速化
    600mm/s
2020-05-02 パラメータの調整
    行き過ぎて壁にぶつかる可能性あり
2020-05-02 バグを修正．
    かなりよくなった．
2020-05-02 パラメータの調整
    加速度は4000mm/sに固定
2020-05-02 直線の加減速も点追従
2020-05-02 最速走行でスタートへ戻る
2020-05-02 Rogyの迷路でパラメータ調整
2020-05-02 左右のスラローム実装
    [Mouse-01.dsn, Mouse-01.kicad_pcb]
2020-05-02 安定したスラローム600m/s
2020-05-02 途中から再開できるように修正
2020-05-02 MazeSolverと新アクションの調整
2020-05-02 誤差の修正方向が逆だった重大バグを修正
    前壁にぶつかる原因だった．
2020-05-02 MoveActionをQueueからMailに変更．
    複数アクションを連続してできるように．
2020-05-02 直線をより高速に
2020-05-02 スタート時にしっかりゼロ補正
2020-05-02 斜め走行
2020-05-02 リフレクタのキャリブレーションを実装
    スタートポジションの左右の壁でキャリブレーション
2020-05-02 軌道生成用のMATLABスクリプト
2020-05-02 横ずれ修正パラメータの調整
    未確認
2020-05-02 軌道追従コードの一般化，左右実装
2020-05-02 横壁補正安定性の向上
2020-05-02 安定化．迷路探索可
    [data.csv]
2020-05-02 本番環境で動いた
2020-05-02 位置の積分を短冊積分から台形積分に変更
2020-05-02 機体パラメータの更新(タイヤ径など)
2020-05-02 絶対座標系で動作確認．
2020-05-02 迷路全体の座標を右向きをx前向きをyとする．
2020-05-02 概形を作成
2020-05-02 MicroMouse2016から移植
2020-05-02 4545用MATLABスクリプト
    [data.csv]
2020-05-02 KiCadデータの名前をKERISEv1に変更
    [AXIS_SENSOR.sch, COM.sch, IR_LED.sch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]
2020-05-02 KERISEv2から移植
2020-05-02 コードの改良
2020-05-02 最速走行をひとつながりの点列の追従に．
    コードを大幅に変更
2020-05-02 fastRunのインターフェースを実装
2020-05-02 180度ターンを生成，90度ターンも2パターン
    [data.csv]
2020-05-02 小さな変更
2020-05-02 MATLABで軌跡を改良
    なめらかに．
    角加速度と最大角速度を統一
    [data.csv]
2020-05-02 探索走行のカーブを緩やかに
    [data.csv]
2020-05-02 curve45Rのバグ修正
2020-05-02 回路図を修正
    電源スイッチにPchFETを挿入
    赤外線LED用FETのゲートをプルダウン
    [AXIS_SENSOR.sch, COM.sch, IR_LED.sch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]
2020-05-02 add kicad .gitignore
    [AXIS_SENSOR.sch, COM.sch, IR_LED.sch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]
2020-05-02 remove generated files
    [KERISEv1.drl, Mouse-01-B.Cu.gbl, Mouse-01-B.Mask.gbs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]
